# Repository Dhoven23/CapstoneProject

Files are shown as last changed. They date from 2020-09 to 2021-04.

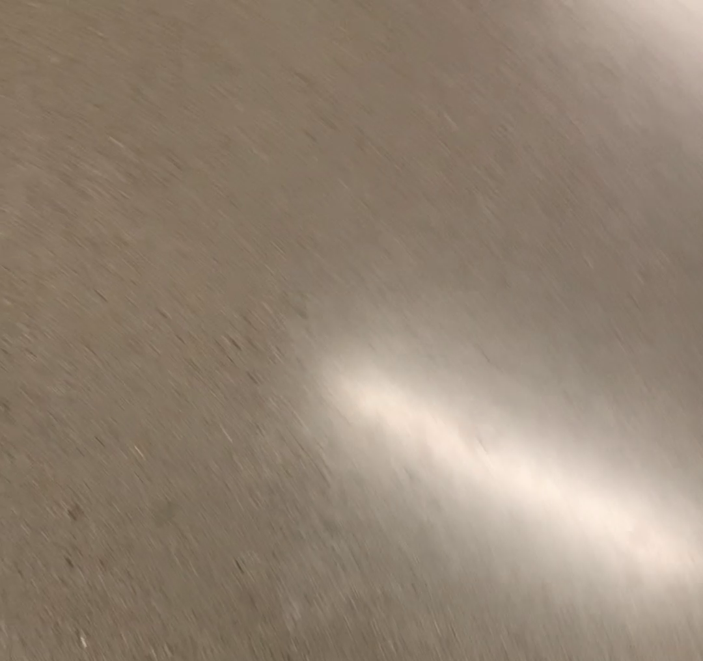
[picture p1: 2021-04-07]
src/opticalfb.png

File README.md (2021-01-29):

# CapstoneProject
Repo for Engineering capstone project

# How to use
This repository is based around the construction of a fully and partially autonomous quadcopter, mostly for educational purposes. The primary goal as a user is to solve as many problems as you feel competent to solve, and thereby improve your knowledge until you can run the vehicle entirely on your own software. Perhaps this vehicle has no advantages over existing drones, but it's far more customizable, and most importantly, its your code!

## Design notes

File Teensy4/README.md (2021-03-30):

# teensyDrone
Extension of CapstoneProject repo
For pull requests, use this version

# Usage

To use this project, you must have:

1. A Raspberry pi 4 with 8GB of memory
2. A Teensy 4.0
3. A 4 channel ESC
4. A BNO055 IMU
5. A TFMini Plus Lidar (or equivalent)
6. 4s brushless motors
7. a frame of your choice (files included)

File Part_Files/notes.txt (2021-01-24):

Here are the solidworks files for the mechanical buidl of the project. The stl's are also provided if you wish to 3D print any part. Feel free to contribute any ideas or improvements to the existing designs.

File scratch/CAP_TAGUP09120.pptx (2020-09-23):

## SPLV01 Weekly Tag Up

Presenter: Carter Senechal
Date: 091420

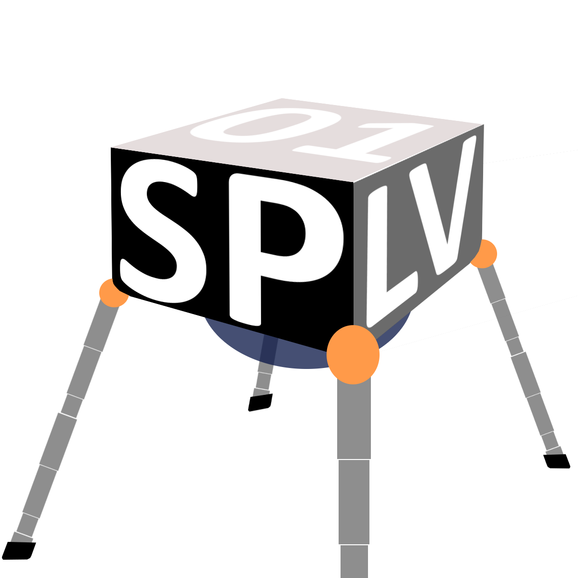
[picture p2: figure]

## Summary

- Meeting Schedule
- Upcoming deadlines
- Responsibility and Roles Hierarchy
- Open Action Items
- MBSE Design Process
- Requirements and Verification
- Jira
- Confluence

## Meeting Schedule

- Need to insert MTG schedule

## Upcoming Deadlines

## Roles and Responsibilities

Daniel Hoven
Phone: 602-696-1426
Email: Daniel.Hoven@gcu.edu
Roles: Team Leader, Chief Engineer
Responsibilities:
• Hold team members accountable to
responsibilities
• Main contributor and manager of code
base and software performance.
• Initiate and vet solutions to problem
definitions, and author technical papers
• answer technical questions, and difficult
inquiries about “big picture” items.
• Responsible for overall team progress, and
failures to meet high level deadlines

Carter Senechal
Phone: (602) 320 – 6890
Email: Cartersenechal@gmail.com
Roles: Project Manager, Systems Engineer, Electrical Engineer
Responsibilities:
• Deriving requirements from stakeholders, and extracting action plan
• Providing verification for project requirements
• Design and build electrical solutions like power and sensor circuits
• Responsible for defining completion criteria, and failures to meet low level deadlines
• POC for status / schedule / general questions

Kevin Alvarado
Phone: (805)722-0993
Email: kevinalvarado12370@gmail.com
Roles: Scheduling manager, mechanical engineer
Responsibilities:
• Responsible for coordinating team member
schedules for meetings, assignment clc’s,
and mentor meetings.
• Implement mechanical designs and
structural engineering solutions
• Responsible for reserving Lab rooms if
needed.

Dawit Feshastion
Phone :(602) 800-2549
Email: dawiterke@gmail.com
Roles: Scheduling manger, mechanical
engineer
Responsibilities:
• Responsible for the project finance
and purchasing department.
• Responsible for material quality and
simulation
• Analysis circuit and instrumental
measurement

## Roles Hierarchy

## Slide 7

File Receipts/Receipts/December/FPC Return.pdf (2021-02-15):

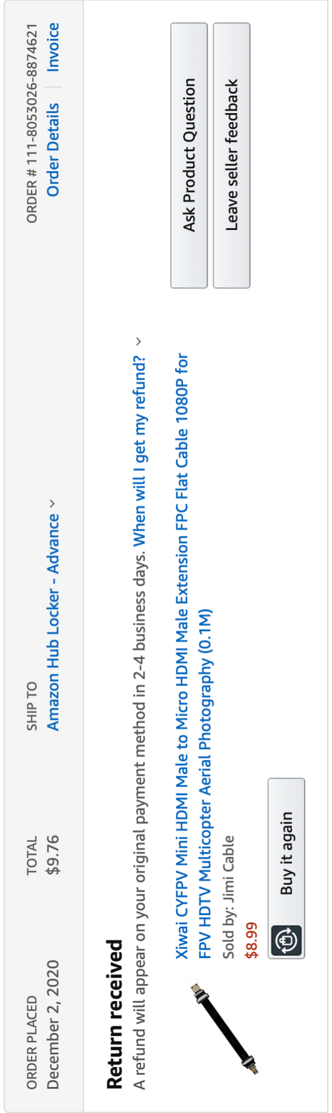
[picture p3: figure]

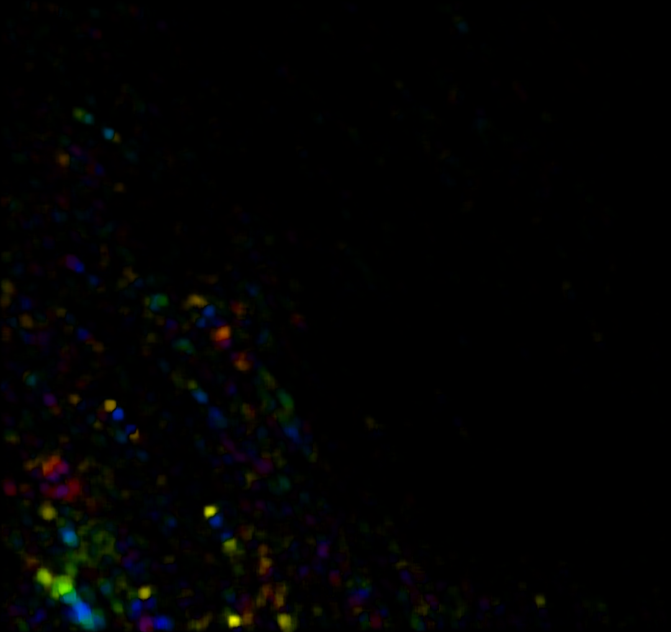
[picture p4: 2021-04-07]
src/opticalhsv.png

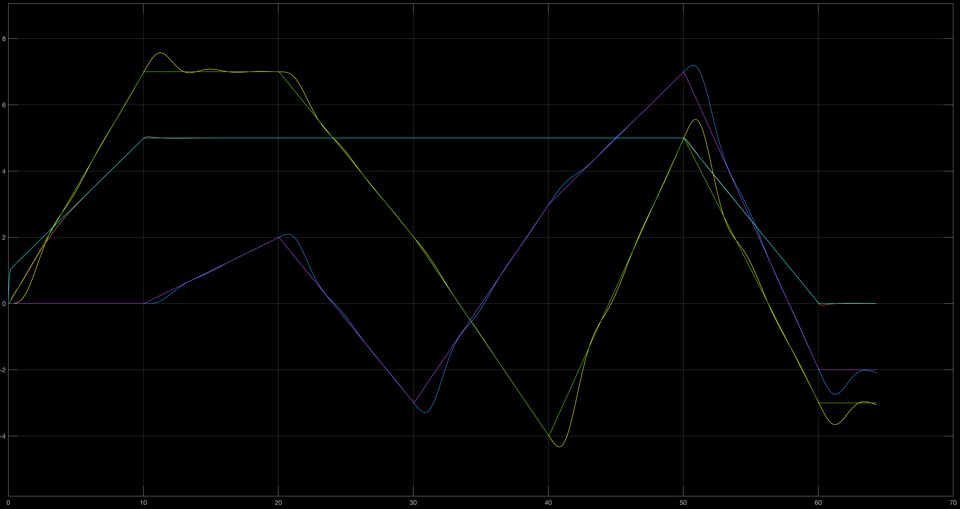
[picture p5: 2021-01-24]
MATLAB/Tracking.png

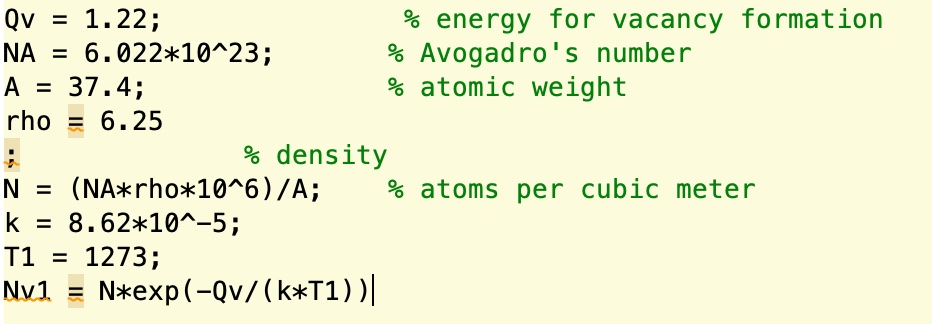
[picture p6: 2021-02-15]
Receipts/Receipts/January/sav.jpg

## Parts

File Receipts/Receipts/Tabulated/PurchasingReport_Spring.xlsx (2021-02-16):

Name | cost | number | total cost | tax | amount paid | Vendor | Date Shipped
Adafruit 9-DOF IMU BNO05 | $34.99 | 1 | $34.99 | $3.01 | $38.00 | Amazon | 2020-10-25
TOF- Lidar TFMini-s | $39.09 | 1 | $39.09 | $3.36 | $42.45 | Amazon | 2020-10-25
Raspberry Pi 4 B (8GB) | $88.86 | 1 | $88.86 | $7.64 | $96.50 | Amazon | 2020-10-22
Teensy 4.0 (/w/ pins) | $29.20 | 1 | $29.20 | $2.51 | $31.71 | Amazon | 2020-10-25
Mechanical Pro H510 Bluetooth Controller | $30.99 | 1 | $30.99 | $2.67 | $33.66 | Amazon | 2020-10-25
WayinTop Jumper wire kit for breadboard | $10.99 | 2 | $21.98 | $1.90 | $23.88 | Amazon | 2020-10-25
Crazepony EMAX 2600kv Brushless Motor (4pcs) | $50.99 | 1 | $50.99 | $4.39 | $55.38 | Amazon | 2020-11-05
Zeee 5200 mAh 50C 11.1V 3S Lipo Battery | $32.99 | 2 | $65.98 | $5.68 | $71.66 | Amazon | 2020-11-09
Aluminium Sheet 6061-T6 | $18.99 | 1 | $18.99 | $1.63 | $20.62 | Amazon | 2020-11-09
M4 Screw Assortment kit | $18.99 | 1 | $18.99 | $1.63 | $20.62 | Amazon | 2020-11-09
Maple Lumber (3/4" x 2" x 12") | $14.20 | 5 | $71.00 | $6.10 | $77.10 | Amazon | 2020-11-09
Degraw 5kg Load cell /w/ amplifier ADC | $12.99 | 4 | $51.96 | $4.48 | $56.44 | Amazon | 2020-11-09
Venom 2-8S Battery monitor | $10.99 | 1 | $10.99 | $1.01 | $12.00 | Amazon | 2020-11-09
USB C LAN adapter (thunderbolt 3 to Gigabit eth) | $17.99 | 1 | $17.99 | $1.55 | $19.54 | Amazon | 2020-11-10
NVIDIA Jetson Nano | $119.00 | 1 | $119.00 | $10.23 | $129.23 | Amazon | 2020-11-11
T300 Jetson Nano Computer Case | $28.99 | 1 | $28.99 | $4.45 | $33.44 | Amazon | 2020-11-11
Wireless-AC8265 Dual mode wireless NIC M.2E Adapter | $22.79 | 1 | $22.79 | $0.00 | $22.79 | Amazon | 2020-11-11
M6 Hex Socket Screw (304 Stainless Steel) | $7.99 | 1 | $7.99 | $0.69 | $8.68 | Amazon | 2020-11-11
Deans to XT60 adapter | $7.99 | 1 | $7.99 | $0.69 | $8.68 | Amazon | 2020-11-19
YUFAY (4CW 4CCW) Tri blae propellers | $11.99 | 1 | $11.99 | $0.00 | $11.99 | Amazon | 2020-11-16
Parallel Y splitter (battery connectors) | $13.09 | 1 | $13.09 | $0.00 | $13.09 | Amazon | 2020-11-16
62 Pcs T-Plug LiPo battery connection fittings | $15.59 | 1 | $15.59 | $0.00 | $15.59 | Amazon | 2020-11-16
30A Brushless ESC with 3A UBEC (3.5mm bullet plugs) | $16.49 | 3 | $49.47 | $0.00 | $49.47 | Amazon | 2020-11-16
Makerfocus I2C 16 channel PWM Servo Controller | $12.99 | 1 | $12.99 | $0.00 | $12.99 | Amazon | 2020-11-09
Solderable breadboards (5 pack + 1 mini board) | $11.99 | 1 | $11.99 | $0.00 | $11.99 | Amazon | 2020-11-09
30A Brushless ESC with 3A UBEC (3.5mm bullet plugs) | $16.49 | 1 | $16.49 | $0.00 | $16.49 | Amazon | 2020-11-17
Parallel Y splitter (battery connectors) | $13.09 | 1 | $13.09 | $12.46 | $25.55 | Amazon | 2020-11-16
Gold Bullet conectors (3.5mm) | $6.98 | 1 | $6.98 | $0.60 | $7.58 | Amazon | 2020-12-07
Geekworm T300 SSD/HDD Jetson Nano shields | $32.89 | 1 | $32.89 | $2.83 | $35.72 | Amazon | 2020-12-10
Mini HDMI FPC ribbon cable | $8.99 | 1 | $8.99 | $0.77 | $9.76 | Amazon | 2020-02-02
Lipo Battery Balance charger | $59.99 | 1 | $59.99 | $0.00 | $59.99 | Amazon | 2020-12-04
ESC programming card | $14.99 | 1 | $14.99 | $6.45 | $21.44 | Amazon | 2020-12-04
3D Printing Job | $6.21 | 1 | $6.21 | $0.00 | $6.21 | GCU Engineering Shop | N/A
3D Printing Job | $23.76 | 1 | $23.76 | $0.00 | $23.76 | GCU Engineering Shop | N/A
3A UBEC | $14.99 | 1 | $14.99 | $1.29 | $16.28 | Amazon | 2021-01-16
4S Batteries (14.8 V. 120 C, 2200 mAh) | $56.99 | 1 | $56.99 | $4.90 | $61.89 | Amazon | 2021-01-13
60A V2 ESC (32 bit) | $81.99 | 1 | $81.99 | $7.05 | $89.04 | Amazon | 2021-01-13
Ball End Mill (1/4" shank, 3/4" Length) | $21.99 | 1 | $21.99 | $1.89 | $23.88 | Amazon | 2021-01-14
Barometer (JBtek BMP180) | $5.99 | 1 | $5.99 | $0.52 | $6.51 | Amazon | 2021-01-14
BNO055 (Adafruit 9DOF IMU fusion) | $34.95 | 1 | $34.95 | $3.01 | $37.96 | Amazon | 2021-01-23
GoPro 50-in-1 Accessory Kit | $29.99 | 1 | $29.99 | $2.58 | $32.57 | Amazon | NYS
GoPro Hero8 (4K Waterproof camera) | $259.99 | 1 | $259.99 | $22.36 | $282.35 | Amazon | 2021-01-24
M Series Taps (Rocaris, M3 M4 M5 M6 M8, Ti Hss Flute) | $13.99 | 1 | $13.99 | $1.20 | $15.19 | Amazon | 2021-01-14
M 2.5 Standoffs (Hex brass spacer assortment) | $12.99 | 1 | $12.99 | $1.12 | $14.11 | Amazon | 2021-01-12
M3 Brass Standoffs (300 pc brass spacer assortment) | $17.99 | 1 | $17.99 | $1.55 | $19.54 | Amazon | 2021-01-23
M3 Screws (500 pc, stainless steel assortment) | $13.99 | 1 | $13.99 | $1.20 | $15.19 | Amazon | NYS
Motors (1800kV, quad) | $129.99 | 1 | $129.99 | $11.18 | $141.17 | Amazon | 2021-01-13
MPU6050 (Diymore 6DOF) | $5.99 | 1 | $5.99 | $0.52 | $6.51 | Amazon | 2021-01-14
Raspberry Pi Camera Module (V2 1080P) | $28.59 | 1 | $28.59 | $2.46 | $31.05 | Amazon | 2021-01-13
Prototyping Boards and Wire (Fermerry 10 gauge wire and AUSTOR 100 pc board kit) | $49.27 | 1 | $49.27 | $34.28 | $4.24 | Amazon | 2021-01-14
Scale (American Fristaden Lab Precision Analytical Balance 10 kg) | $119.00 | 1 | $119.00 | $10.23 | $129.23 | Amazon | 2021-01-13
Soldeirng Flux (Rosin Paste Flux 2oz) | $9.02 | 1 | $9.02 | $0.78 | $9.80 | Amazon | 2021-01-21
Teensy 4.0 (w/ pins) | $29.00 | 2 | $58.00 | $4.98 | $62.98 | Amazon | 2021-01-14
TF Mini-S LiDAR Lase Range Sensor | $41.99 | 1 | $41.99 | $3.61 | $45.60 | Amazon | 2021-01-24
Tooling Batteries (Synergy R9 Dog Collar -2x COMP 4 SAFT batteries) | $13.93 | 1 | $13.93 | $1.20 | $15.13 | Amazon | 2021-01-20
Flow Breakout Board (1597-1550-ND) | $40.80 | 1 | $40.80 | $4.08 | $44.88 | DigiKey | 2021-01-13
SD Cards (SanDisk 128GB micro) | $19.99 | 4 | $79.96 | $6.88 | $86.84 | Amazon | NYS
TOTAL: |  |  |  |  | $2315.94
BUDGET USAGE: |  |  |  |  | 57.90%

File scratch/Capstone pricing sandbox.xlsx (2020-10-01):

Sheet: big version
 | Main Battery |  | Main Computer |  | Main Power Unit | Secondary power unit
Power capacity (mAh) | 10000 | Price | $400 | part | 70 mm EDF
Voltage | 22.2 | Power Consumption (W max) | 50 | price | $65
C discharge rate | 20 | Weight (kg) | 0.75 | weight (g) | 256
price | 100 |  |  | Amperes | 69.81981982
number | 2 |  |  | power consumption (W) | 1550
weight (g) | 1320 |  |  | number | 4
instant current | 500.0 |  |  | thrust output (g) | 2500
total instant power delivery | 22200 |  |  | total mass | 1024
total price | 200 |  |  | total power consumption | 6200
total weight (kg) | 2.64 |  |  | total cost | $260
 |  |  |  | total thrust remaining (kg) | 8.976
 |  |  |  | Voltage | 22.2
TOTAL LIFT MASS (kg) | 8.976
POWER REQ. (W) | 6200
PAYLOAD REM. (kg) | 5.586
TOTAL PRICE ($) | $860
FLIGHT TIME (sec.) | 257.8064516

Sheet: Little Version (2)
 | Main Battery |  | Item List: | name: | price: | link:
Power capacity (Wh) | 33.3 |  |  | 3s LiPo battery | $60
Voltage | 11.1 |  |  | brushless motors x4 | $120
C discharge rate | 50 |  |  | ESC (30A) x4 | $60
price | $60.00 |  |  | Jetson Xavier nx | $400
number | 1 |  |  | BNO055 IMU (9 axis absolute) | $35 | https://www.amazon.com/Adafruit-Absolute-Orientation-Fusion-Breakout/dp/B017PEIGIG?cv_ct_cx=bno055
weight (g) | 175 |  |  | Carbon Fiber Sheet (3mm) | $100 | https://www.amazon.com/400x500x3-0MM-Carbon-Fiber-Sheet-Twill/dp/B085H7NX4N?hvadid=459474431166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
instant current | 150.0 |  |  | Onyx (3d printing material) 1kg | $180 | https://markforged.com/resources/blog/introducing-our-new-markforged-material-onyx
total instant power delivery (W) | 1665 |  |  | CCF for 3d printing (50cc) | $150 | https://markforged.com/materials/continuous-fibers/continuous-carbon-fiber
total price | $60.00
total weight (kg) | 0.175 |  | Total Price: |  | $1105
Amp Hours | 3
 | Main Computer
Price | $90
Teensy 4.1 MC | $30
Power Consumption (W max) | 15
Weight (kg) | 0.2
 | Main Power Unit | Secondary power unit
part | brushless motor | 30 A esc
price | $25 | $15.00
weight (g) | 52 | 20
Amperes | 13 | 25
power consumption (W) | 144.3 | 125
number | 4 | 4
thrust output (g) | 370
total weight (kg) | 0.208 | 0.08
total power consumption | 577.2 | 500
total cost | $100 | $60.00
total thrust output (kg) | 1.48
Voltage | 11.1 | 5
TOTAL MASS (kg) | 0.663
TOTAL MASS (lb.) | 1.4586
TOTAL LIFT MASS (kg) | 0.817
TOTAL LIFT MASS (lb.) | 1.7974
POWER REQ. (W) | 258.570
PAYLOAD REM. (kg) | 0.442
TOTAL PRICE ($) | $310
FLIGHT TIME (sec.) | 417.2641838
FLIGHT TIME (min.) | 7.0

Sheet: Little Version
 | Main Battery |  | Item List: | name: | price: | link:
Power capacity (Wh) | 61.05 |  |  | 3s LiPo battery | $60
Voltage | 11.1 |  |  | brushless motors x4 | $120
C discharge rate | 140 |  |  | ESC (30A) x4 | $60
price | $60.00 |  |  | Jetson Xavier nx | $400
number | 1 |  |  | BNO055 IMU (9 axis absolute) | $35 | https://www.amazon.com/Adafruit-Absolute-Orientation-Fusion-Breakout/dp/B017PEIGIG?cv_ct_cx=bno055
weight (g) | 416 |  |  | Carbon Fiber Sheet (3mm) | $100 | https://www.amazon.com/400x500x3-0MM-Carbon-Fiber-Sheet-Twill/dp/B085H7NX4N?hvadid=459474431166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
instant current | 770.0 |  |  | Onyx (3d printing material) 1kg | $180 | https://markforged.com/resources/blog/introducing-our-new-markforged-material-onyx
total instant power delivery (W) | 8547 |  |  | CCF for 3d printing (50cc) | $150 | https://markforged.com/materials/continuous-fibers/continuous-carbon-fiber
total price | $60.00 |  |  | New MacBook for Me | 1 kidney | https://www.amazon.com/gp/product/B08821611Y/ref=ox_sc_act_title_1?smid=ATVPDKIKX0DER&th=1
total weight (kg) | 0.416 |  | Total Price: |  | $1105
Amp Hours | 5.5
 | Main Computer
Price | $400
Power Consumption (W max) | 50
Weight (kg) | 0.75
 | Main Power Unit | Secondary power unit
part | 880 kv outrunner edf | 30 A esc
price | $30 | $15.00
weight (g) | 65 | 32
Amperes | 17 | 3
power consumption (W) | 188.7 | 15
number | 4 | 4
thrust output (g) | 900
total weight (kg) | 0.26 | 0.128
total power consumption | 754.8 | 60
total cost | $120 | $60.00
total thrust output (kg) | 3.6
Voltage | 11.1 | 5
TOTAL MASS (kg) | 1.554 | 3.42597948
TOTAL LIFT MASS (kg) | 2.046 | 2.267964547
POWER REQ. (W) | 540.1548387
PAYLOAD REM. (kg) | 0.88
TOTAL PRICE ($) | $640
FLIGHT TIME (sec.) | 406.8833309

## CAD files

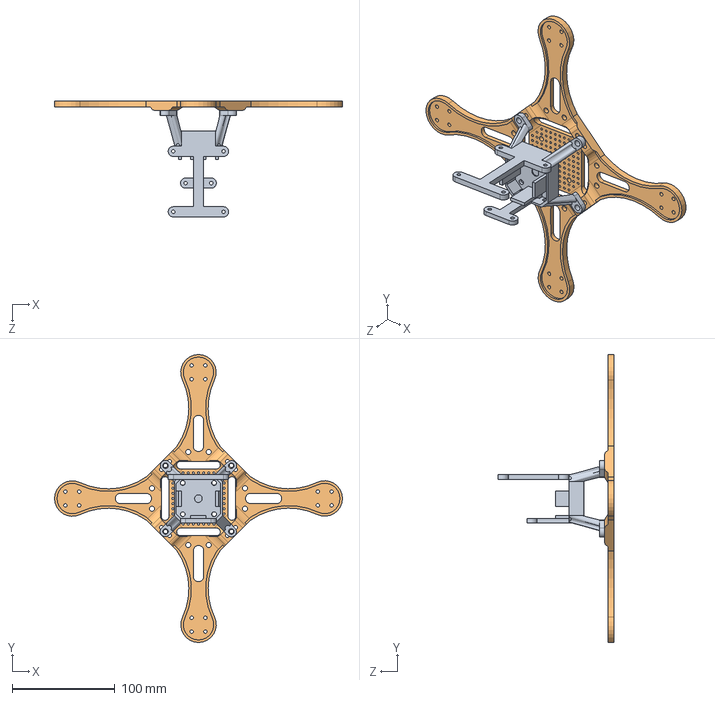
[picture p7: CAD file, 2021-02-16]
Part_Files/Drone 2.0/Assem2.SLDASM
280.7 x 280.7 x 113.0 mm
Superstructure
base plate (Revised holes)

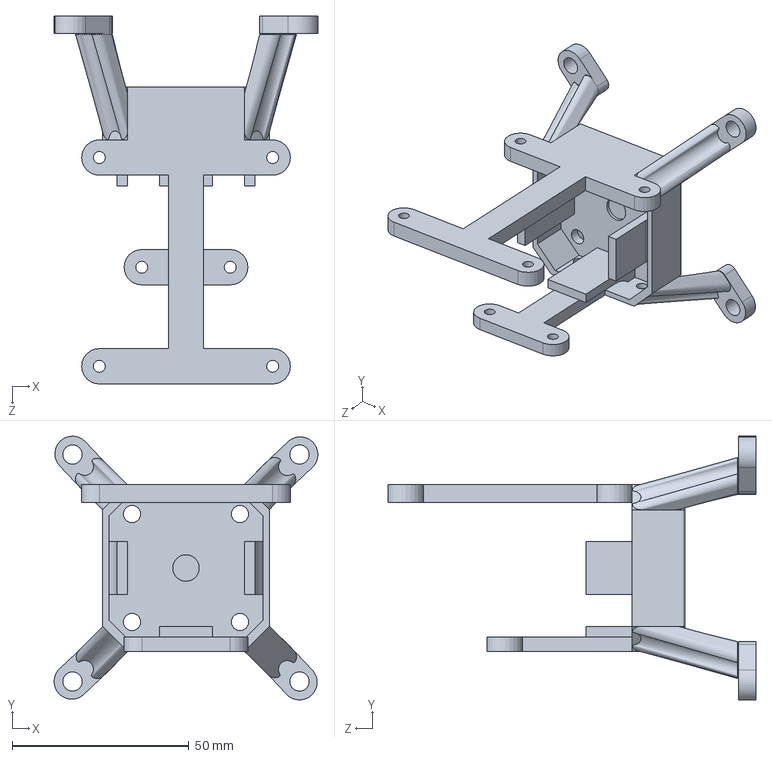
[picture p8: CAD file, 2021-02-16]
Part_Files/Drone 2.0/Superstructure.SLDPRT
74.5 x 74.5 x 104.0 mm

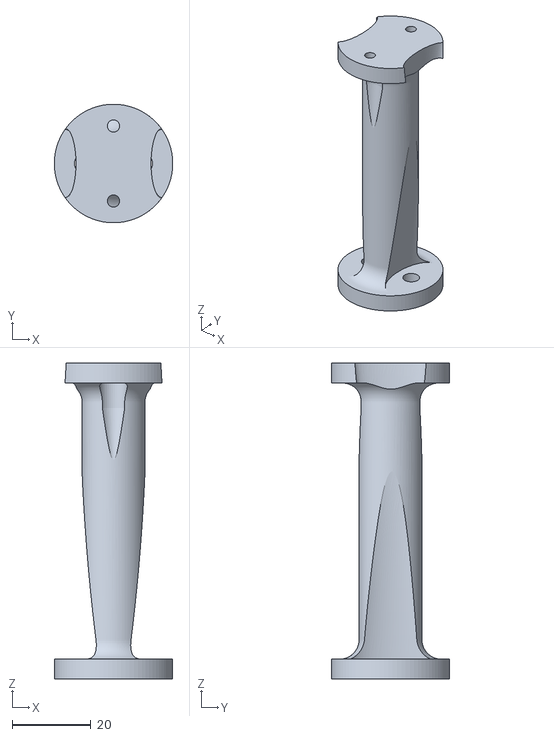
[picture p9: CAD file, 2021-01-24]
Part_Files/Drone 2.0/Force_cell_standoff.STL
30.0 x 30.0 x 80.0

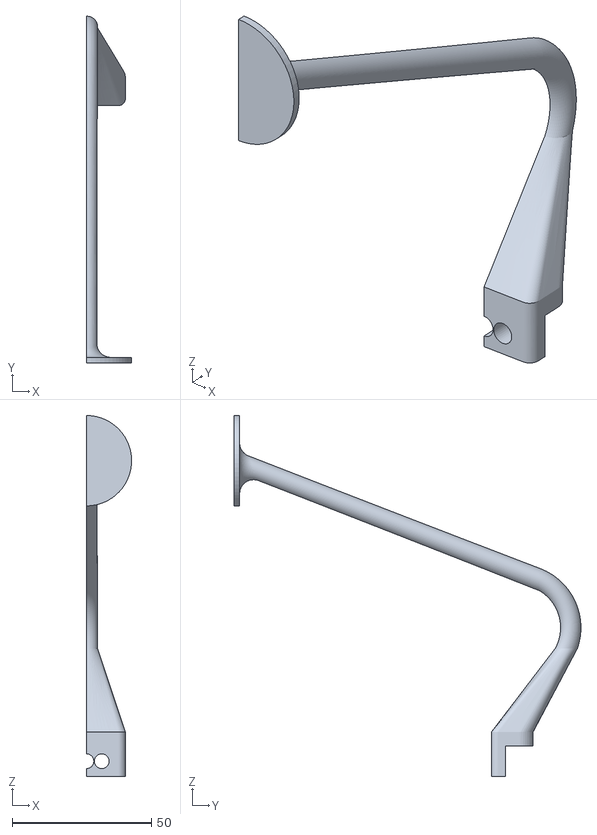
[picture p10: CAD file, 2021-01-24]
Part_Files/Drone 2.0/landing leg1.STL
16.2 x 124.7 x 129.8

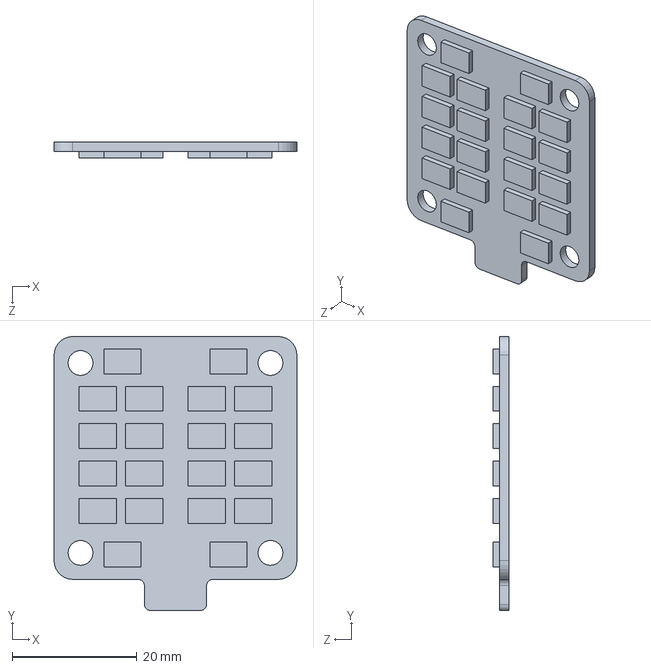
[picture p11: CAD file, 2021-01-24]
Part_Files/Drone 2.0/esc.SLDPRT
39.0 x 44.0 x 2.50 mm

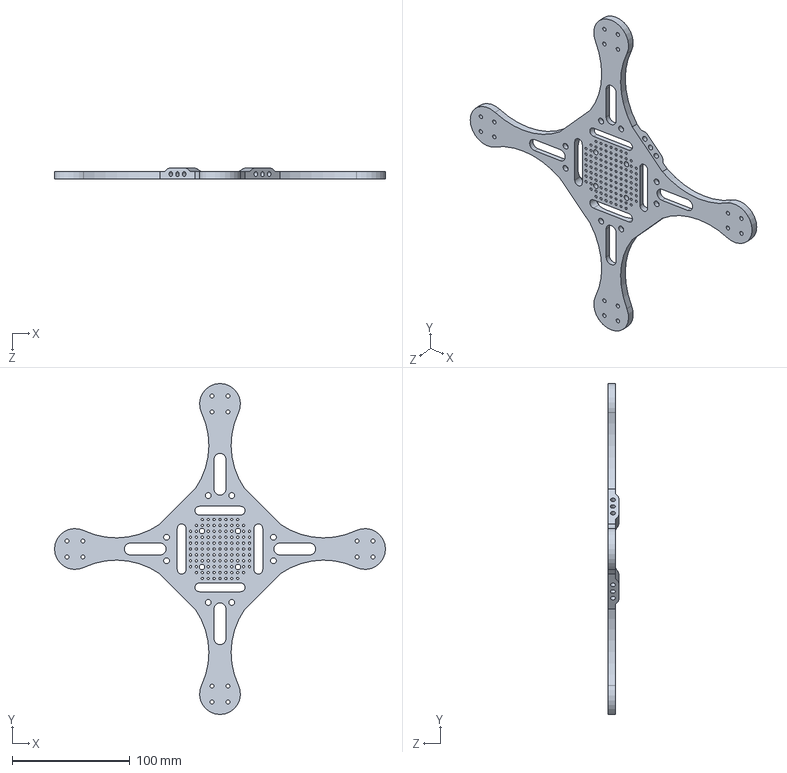
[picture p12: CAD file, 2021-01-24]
Part_Files/Drone 2.0/base plate.SLDPRT
280.7 x 280.7 x 9.00 mm

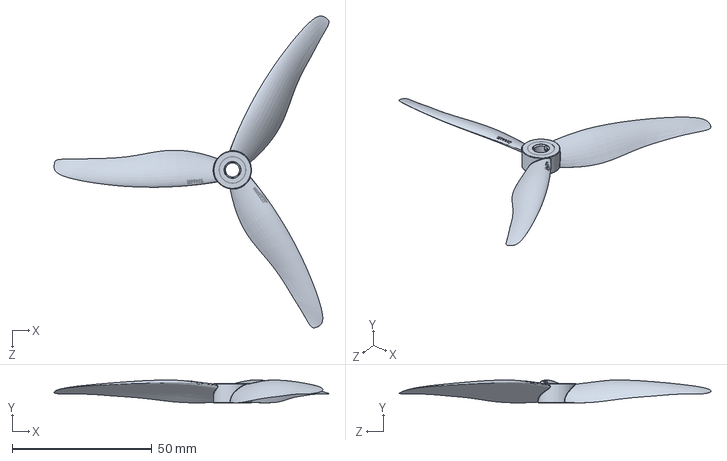
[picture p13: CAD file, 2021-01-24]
Part_Files/Drone 2.0/fan.SLDPRT
98.5 x 8.23 x 111.7 mm

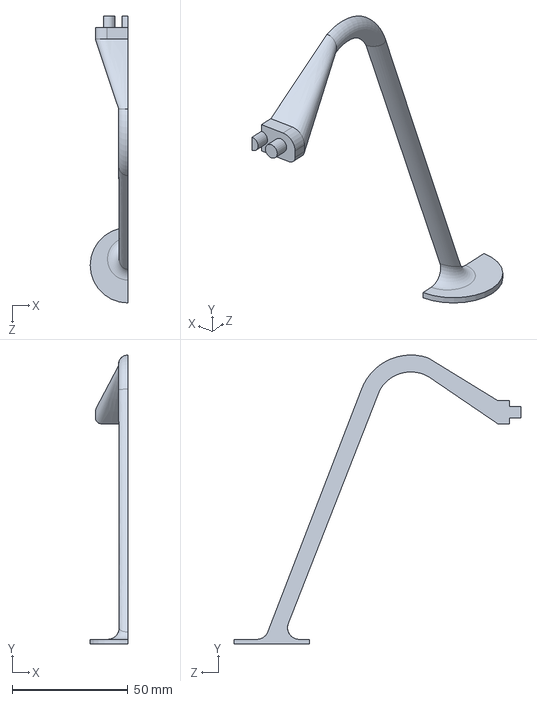
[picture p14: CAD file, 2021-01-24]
Part_Files/Drone 2.0/landing leg2.SLDPRT
16.2 x 124.7 x 123.8 mm

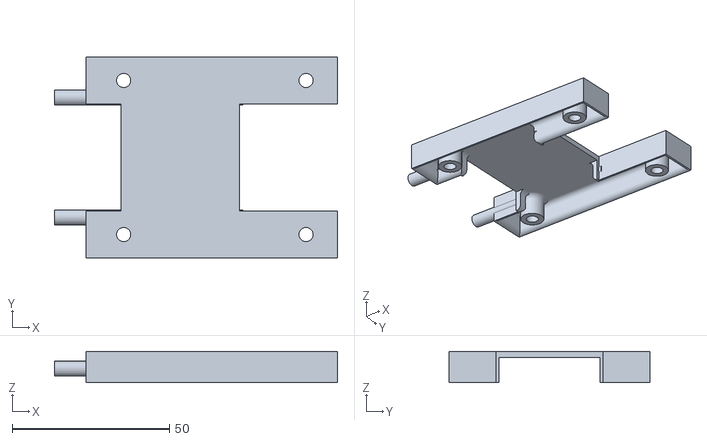
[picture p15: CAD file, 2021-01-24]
Part_Files/Drone 2.0/pi backing.STL
90.0 x 64.0 x 10.0

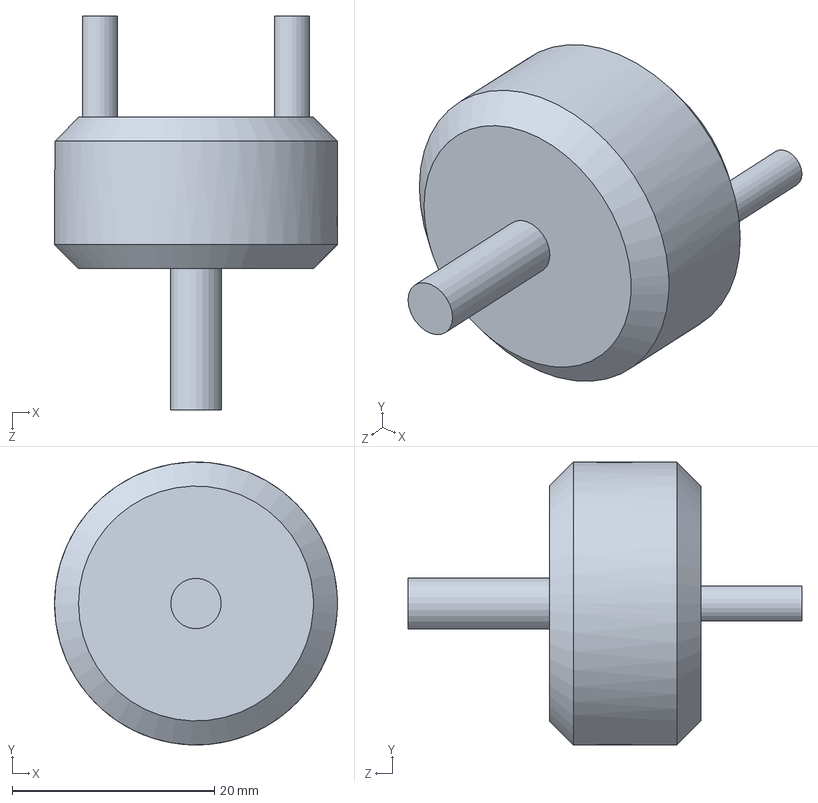
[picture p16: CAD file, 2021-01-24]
Part_Files/Drone 2.0/motor exclusion.SLDPRT
28.0 x 28.0 x 39.0 mm

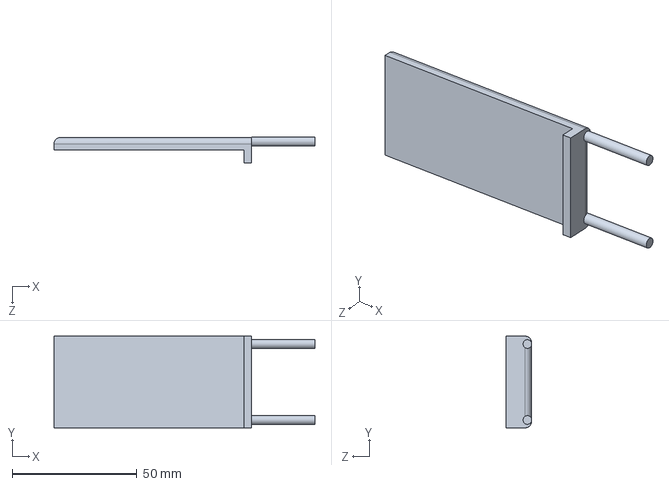
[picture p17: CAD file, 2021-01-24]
Part_Files/Drone 2.0/pcb back.SLDPRT
104.8 x 36.8 x 10.3 mm

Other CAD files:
Part_Files/Drone 2.0/landing leg.SLDPRT
Part_Files/Drone 2.0/force_ce.SLDPRT
Part_Files/Drone 2.0/Superstructure.STL
Part_Files/Drone 2.0/base plate.STL
Part_Files/Drone 2.0/landing leg.STL
Part_Files/Drone 2.0/landing leg2.STL

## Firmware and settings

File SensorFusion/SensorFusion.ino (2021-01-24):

/* This code is free and open source. I only ask that if you use my code in an academic setting, reference it appropriately. 
*  I mean, an extra citation can't hurt can it?
* 
* Author: Daniel Hoven
* Univeristy: Grand Canyon University
* Email: Daniel.Hoven@gcu.edu
*/

/* This code is for sensor fusion of IMU data with barometric altitude 
 *  and accelerometer data for odometric calculation of position. 
 */

// This code relies on the Adafruit Unified Sensor Library

#include <Wire.h>
#include <Adafruit_BMP085.h>
#include <Adafruit_Sensor.h>
#include <Adafruit_BNO055.h>
#include <Adafruit_MPU6050.h>
#include <utility/imumaths.h>


// Adafruit Sensors Initialize
Adafruit_BMP085 bmp;
Adafruit_BNO055 bno = Adafruit_BNO055(55, 0x28);
Adafruit_MPU6050 mpu;


// Declare ext. vars
float acc_x = 0,
      acc_y = 0,
      acc_z = 0,
      vel_x = 0,
      vel_y = 0,
      vel_z = 0,
      pos_x = 0,
      pos_y = 0,
      pos_z = 0,
      alt = 0, 
      alt_old = 0, 
      off_set = 0,
      q0,
      q1,
      q2,
      q3,
      av_alt[10],
      C[4];

float gravity_quaternion[4] = {0, 0, 0, 10.1};

      
// Declare Processor dependent vars.       
volatile float _q0 = 0, 
               _q1 = 1, 
               _q2 = 0, 
               _q3 = 0;
  
void setup() {
  
  Serial.begin(115200);
  delay(100);

  // Initialize Barometer
  if (!bmp.begin()) {
	  Serial.println("Could not find a valid BMP085 sensor, check wiring!");
	  while (1) {
	    delay(10);
	    }
  }

  // Initialize Accelerometer
  if (!mpu.begin()) {
    Serial.println("Failed to find MPU6050 chip");
    while (1) {
      delay(10);
    }
  }

  // Initialize IMU
  if (!bno.begin())
  {
    /* There was a problem detecting the BNO055 ... check your connections */
    Serial.print("Ooops, no BNO055 detected ... Check your wiring or I2C ADDR!");
    while (1){
      delay(10);
    }
  }

  //Set Accelerometer limits
  mpu.setAccelerometerRange(MPU6050_RANGE_8_G);
  mpu.setGyroRange(MPU6050_RANGE_500_DEG);
  mpu.setFilterBandwidth(MPU6050_BAND_21_HZ);
  
  // Get Baseline alititude
  delay(500);
  off_set = bmp.readAltitude(101500);
  delay(1000);
}

  
void loop() {
   
    ReadBarometricAltitude();
    get_IMU_sample();
    get_Accels();

    
    // math for gravity correction
    q0 = _q0;
    q1 = _q1;
    q2 = _q2;
    q3 = _q3;
    
    float gamma  = -atan2(2.0 * (q3 * q2 + q0 * q1) , 1.0 - 2.0 * (q1 * q1 + q2 * q2));// * (180/PI);
    float beta = asin(2.0 * (q2 * q0 - q3 * q1));// * (180/PI);
    float alpha   = -atan2(2.0 * (q3 * q0 + q1 * q2) , - 1.0 + 2.0 * (q0 * q0 + q1 * q1));// * (180/PI);

    float RotationMatrix[3][3];
    
          RotationMatrix[0][0] = cos(alpha)*cos(beta);
          RotationMatrix[1][0] = cos(alpha)*sin(beta)*sin(gamma) - sin(alpha)*cos(gamma);
          RotationMatrix[2][0] = cos(alpha)*sin(beta)*cos(gamma) + sin(alpha)*sin(gamma);
          RotationMatrix[0][1] = sin(alpha)*cos(beta);
          RotationMatrix[1][1] = sin(alpha)*sin(beta)*sin(gamma) + cos(alpha)*cos(gamma);
          RotationMatrix[2][1] = sin(alpha)*sin(beta)*cos(gamma) - cos(alpha)*sin(gamma);
          RotationMatrix[0][2] = -sin(beta);
          RotationMatrix[1][2] = cos(beta)*sin(gamma);
          RotationMatrix[2][2] = cos(beta)*cos(gamma);

//          for(int i=0;i<3;i++){
//            Serial.print("| ");
//            for(int j=0;j<3;j++){
//              Serial.print(RotationMatrix[i][j]),Serial.print(' ');
//            }
//            Serial.println(" |");
//          }

    

    float gravity[3] = {0, 0, 1},
          rot_quat[4] = {q0, q1, q2, q3},
          rot_quat2[4] = {q0,-q1,-q2,-q3},
          rot_gravity[4],
          acc_quat[4] = {0,acc_x,acc_y,acc_z};
                      
          
      
    // Rotate Gravity
    HamiltonProduct(rot_quat, gravity_quaternion);
    HamiltonProduct(C,rot_quat2); 

    // Store output
    for(int i=0;i<4;i++){
      rot_gravity[i] = C[i];
    }

    // Rotate Acceleration
    HamiltonProduct(rot_quat, acc_quat);
    HamiltonProduct(C,rot_quat2);

    for(int i=0;i<4;i++){
      acc_quat[i] = C[i];
    }
    
    
    //acc_x-=rot_gravity[1]; // Remove Gravity (i)
    //acc_y-=rot_gravity[2]; // Remove Gravity (j)
    //acc_z-=rot_gravity[3]; // Remove Gravity (k)

    

    Serial.print(" gravity.x "),Serial.print(rot_gravity[1],2);
    Serial.print(" gravity.y "),Serial.print(rot_gravity[2],2);
    Serial.print(" gravity.z "),Serial.println(rot_gravity[3],2);
    Serial.print(" acc.x: "),Serial.print(acc_x);
    Serial.print(" acc.y: "),Serial.print(acc_y);
    Serial.print(" acc.z: "),Serial.println(acc_z);
    Serial.print(" roll: "),Serial.print(gamma);
    Serial.print(" pitch: "),Serial.print(beta);
    Serial.print(" yaw: "),Serial.println(alpha);
    
    
    //Serial.print(", Alt: "),Serial.print(alt*100),Serial.println(" cm");
    
    delay(10);
}


void get_IMU_sample() {
  /* get quaternions */
  imu::Quaternion quat = bno.getQuat();
  

  _q0 = quat.w();
  _q1 = quat.x();
  _q2 = quat.y();
  _q3 = quat.z();
  
}

void ReadBarometricAltitude(){
  
    alt = bmp.readAltitude(101500) - off_set;
    
    float num = 0;
    
    for(int i = 0;i<9;i++){ av_alt[i] = av_alt[i+1]; num+=av_alt[i];}
    
    av_alt[9] = alt;
    num+=alt;
    alt=num/50; 
    
    
}

void get_Accels(){

    sensors_event_t a, g, temp;
    mpu.getEvent(&a, &g, &temp);
 
    acc_x = a.acceleration.x;
    acc_y = a.acceleration.y;
    acc_z = a.acceleration.z;
}

void HamiltonProduct(float A[4], float B[4]){

    float a1 = A[0], //input quaternion A
          a2 = A[1], // (i)
          a3 = A[2], // (j)
          a4 = A[3]; // (k)

    float b1 = B[0], //input quaternion B
          b2 = B[1], // (i)
          b3 = B[2], // (j)
          b4 = B[3]; // (k)
          
    
    float c1 = a1*b1 - a2*b2 - a3*b3 - a4*b4, // Output Quaternion (w)
          c2 = a1*b2 + a2*b1 + a3*b4 - a4*b3, // Output Quaternion (i)
          c3 = a1*b3 - a2*b4 + a3*b1 + a4*b2, // Output Quaternion (j)
          c4 = a1*b4 + a2*b3 - a3*b2 + a4*b1; // Output Quaternion (k)
          
    C[0] = c1;
    C[1] = c2;
    C[2] = c3;
    C[3] = c4;

}

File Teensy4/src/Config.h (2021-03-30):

/* =========================================================================================
  Define controller constants */

#define THROTTLE_SCALER 0.5
#define kp 2                               // Altitude PID proportional constant 
#define ki 0                              // Altitude PID integral constant
#define kd 0.01                          // Altitude PID derivative constant
#define filtAlt 0.95                    // Altitude Estimation Filter constant (0-1)
#define LQRmult 0.45                   // Scaling factor for control law, varies between 0.5-1
#define LQR_P 0                     // LQR_P constant proportional prescaler
#define LQR_E 1.75                   // Integrator prescaler
#define INTEGRATOR_CLAMP 0.175      // Clamping term for integrator 
#define SLEW_LIMIT 10              // controller gimbal limit (higher = faster vehicle)
#define SLEW_FILTER 0.25           // Controller rate limiter (0-1), higher = slower/stabler
#define D_COMP 0.1             // dynamic damping coefficient. higher = more dynamic, lower = more damping
#define V_SPD 0.01              // Vertical speed reduction rate (depends on iteration time, faster code = lower value, typically 0.001-0.01)
#define DERIVATIVE_FILT 0.75   // Fintering term for low pass derivative filter

/* ==========================================================================================
  Define communication setup
*/
#ifndef RADIO_BAUDRATE
#define RADIO_BAUDRATE 57600    // Telemetry radio baudrates (use 57600)
#endif

#define LIDAR_BAUDRATE 115200   // LiDAR sensor UART speed. default is 115200

#ifndef USB_BAUDRATE
#define USB_BAUDRATE 250000     // USB Serial port baudtate. (N/A for USB mode)
#endif

#ifndef SERIAL_USB
#define SERIAL_USB Serial       // Serial port for USB communication (always Serial)
#endif

#ifndef RADIO_SERIAL
#define RADIO_SERIAL Serial4    // Serial port for radio communication
#endif

#ifndef LIDAR_SERIAL
#define LIDAR_SERIAL Serial1    // Serial port for LiDAR sensor
#endif

#define CMD_SERIAL Serial      // Listen port for waypoints
#define TELEMETRY1 Serial4     // wireless telemetry
#define TELEMETRY2 Serial      // wired telemetry

/* ==========================================================================================
  Define motor setup */

#define ESC1 6         // Pin for ESC1
#define ESC2 7         // Pin for ESC2
#define ESC3 5         // Pin for ESC3
#define ESC4 4         // Pin for ESC4
#define MAXVAL 1500    // highest speed controller may command esc
#define MINVAL 900     // lowest speed controller may command esc (other than 0)
#define IDLE_SPEED 20  // idle motor speed, range 12-20 ish, depending on esc calibration

#define E1CENTER 1         // Pin for ESC1
#define E2CENTER 1         // Pin for ESC2
#define E3CENTER 1         // Pin for ESC3
#define E4CENTER 1         // Pin for ESC4

/* Set the delay between iterations */
#define MAIN_DELAY 1

/* Define LQR gain matrix.
The rows define the inputs (U) to each Output value
The columns are the Full state (X) of the Vehicle
The linear math here is: 
                X' = AX 
                + K(R-X) 
                + K(R-Xint)

The Expansion of U is:
                        U[0] = total vehicle thrust
                        U[1] = moment about the X axis
                        U[2] = moment about the y axis
                        U[3] = moment about the z axis

So to "tune" and axis, say x, find the corresponding row, 
in this case the second row, and alter the values 
to choose how the moment about that axis is related to 
the respective columns of the vehicles state. (Curently the values
represent response to angular position about X, and angular speed about X)
*/

double K [4][6] = {{
    0, 0, 0, 0, 0, 0,
  }, {
    15, 0, 0, -100, 0, 0,
  }, {
    0, 15, 0, 0, -100, 0,
  }, {
    0, 0, 15, 0, -30, 0,
  },
};

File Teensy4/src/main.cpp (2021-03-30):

#include <Arduino.h>
#include "SensorFunctions.h"

/* --------------------------------------------------------------------------------------
  Main Controller Code to run on Teensy 4.0
  Author: Daniel Hoven Date: 3/15/2021 Project: Senior Capstone
  --------------------------------------------------------------------------------------*/
/*= == == == == == == == == == == == == == == == == == == == == == == == == == == == == == == == == = == == == == == == == =
SETUP 
*/

void setup()

{
  /* Open Serial Ports*/

  SERIAL_USB.begin(250000);
  LIDAR_SERIAL.begin(115200);
  RADIO_SERIAL.begin(RADIO_BAUDRATE);
  delay(100);

  /* put liDAR in std. output mode */

  set_liDAR();

  while (!bno.begin())
  {
    /* There was a problem detecting the BNO055 ... check your connections */
    SERIAL_USB.print("Ooops, no BNO055 detected ... Check your wiring or I2C ADDR!");
    delay(200);
  }

  SERIAL_USB.print("IMU found\n");
  bno.setExtCrystalUse(true);

  for (int i = 0; i < 4; i++)
  {
    for (int j = 0; j < 6; j++)
    {
      K[i][j] *= LQRmult;
    }
  }

  calibrateESCs();
  delay(500);
}

/*-------------------------------------------------------------------------------
   main
  ------------------------------------------------------------------------------*/
void loop(void)
{

  global.dt = micros() - global.tMicros;
  global.tMicros = micros();
  global.dt = global.dt / 1000000;

  get_IMU_sample(global.dt,global.iterations),
  get_Distance_sample(global.dt),
  ELQR_calc();

  if (global.VERT_SPEED == true)
  {
    vertSpeedHold();
  }
  receiveData();

  if (global.iterations % 5 == 0)
  {
    printData();
    //printTestData();
  }

  // Make sure Vehicle isn't dying
void CheckAttitudeLimits(); // Oh Sh*t method

  if ((global.TAKEOFF_FLAG) && (millis() > 2000))
  {
    IntegralTracker(global.dt);
    AltitudePID();
  }

  if (global.iterations < 1000)
  {
    for (int i = 1; i < 4; i++)
    {
      signal.Ucal[i] = signal.U[i];
    }
  }
  else
  {
    if (!global.STOP_FLAG)
    {
      commandESCs();
    }
    else
    {
      STOP();
    }
  }
  global.iterations++;
  delay(MAIN_DELAY);
}

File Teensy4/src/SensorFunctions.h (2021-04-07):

#include "Config.h"
#include "Arduino.h"
#include <Wire.h>
#include <Adafruit_Sensor.h>
#include <Adafruit_BNO055.h>
#include <utility/imumaths.h>
#include <avr/io.h>
#include <avr/interrupt.h>
#include <Servo.h>

/* ==========================================================================================
  Declare globals */

struct Signal
{
  float e1 = 0,
        e2 = 0,
        e3 = 0,
        e4 = 0,
        Ecal[4] = {0, 0, 0, 0};
  
  int throttle = 0;

  double U[4] = {IDLE_SPEED, 0, 0, 0},
         Ucal[4];

};

volatile float liDARold = 0,
               _lidar = 0;

volatile int liDARval = 0,
             strength = 0;

struct Euler
{
  double x = 0,
         y = 0,
         z = 0;

  double dx = 0,
         dy = 0,
         dz = 0;

  double Hist[3][5];
};

struct State
{
  double Full[6] = {0, 0, 0, 0, 0, 0},
         Integral[6],
         Old[6],
         Error[6];
};

struct Altitude
{
  double alt = 0,
         d_alt = 0,
         initAlt = 0;
};

struct Setpoint
{
  double R[6] = {0, 0, 0, 0, 0, 0};
  double Alt = 0;
  double Rcal[3] = {0, 0, 0};
  double verticalSpeed = 0;
};

struct Global
{
  long int iterations = 0;
  int tMicros = 0;
  double dt = 0;

  String STATE = "STARTUP";

  bool STOP_FLAG = false,
       TAKEOFF_FLAG = false,
       VERT_SPEED = true;
};

float Ncode;
u_int16_t counter = 0;

String STATE = "STARTUP";

char Dcode[3];

State X;           // Vehicle Full state struct
Euler euler;       // Euler angle struct
Setpoint setPoint; // setpoint struct
Altitude altitude; // altitude data
Signal signal;     // controller output data
Global global;

/* =========================================================================================
  Declare Sensor Connections on I2C bus
*/

Adafruit_BNO055 bno = Adafruit_BNO055(55, 0x28);

Servo esc1,
    esc2,
    esc3,
    esc4;

/*-------------------------------------------------------------------------
   Write external functions
  ---------------------------------------------------------------------------*/

void set_liDAR()
{
  LIDAR_SERIAL.write(0x42);
  LIDAR_SERIAL.write(0x57);
  LIDAR_SERIAL.write(0x02);
  LIDAR_SERIAL.write(0x00);
  LIDAR_SERIAL.write(0x00);
  LIDAR_SERIAL.write(0x00);
  LIDAR_SERIAL.write(0x01);
  LIDAR_SERIAL.write(0x06);
}

void calibrateESCs()
{

  esc1.attach(ESC1);
   esc2.attach(ESC2);
    esc3.attach(ESC3);
     esc4.attach(ESC4);
      delay(100);
     esc1.write(30);
    esc2.write(30);
   esc3.write(30);
  esc4.write(30);
  delay(1000);

  for (int i = 30; i > 20; i--)
  {
    esc1.write(i);
    esc2.write(i);
    esc3.write(i);
    esc4.write(i);
  }

  for (int i = 20; i < 35; i++)
  {
    esc1.write(i);
    esc2.write(i);
    esc3.write(i);
    esc4.write(i);
    delay(150);
  }
  delay(2000);
  esc1.write(40);
  esc2.write(40);
  esc3.write(40);
  esc4.write(40);
  delay(2000);
}

FASTRUN void get_IMU_sample(double dt, double iterations)
{

  /* get quaternions */

  imu::Quaternion quat = bno.getQuat();

  volatile double q0 = quat.w();
  volatile double q1 = quat.x();
  volatile double q2 = quat.y();
  volatile double q3 = quat.z();

  //quaternion conversion

  euler.x = (-setPoint.Rcal[0]) - atan2(2.0 * (q3 * q2 + q0 * q1), 1.0 - 2.0 * (q1 * q1 + q2 * q2));  //* (180/PI);
  euler.y = (-setPoint.Rcal[1]) + asin(2.0 * (q2 * q0 - q3 * q1));                                    // * (180/PI);
  euler.z = (-setPoint.Rcal[2]) - atan2(2.0 * (q3 * q0 + q1 * q2), -1.0 + 2.0 * (q0 * q0 + q1 * q1)); //* (180/PI);

  for (int i = 0; i < 6; i++)
  {
    X.Old[i] = X.Full[i];
  }

  X.Full[0] = euler.x;
  X.Full[1] = euler.y;
  X.Full[2] = euler.z;

  // Compute Derivatives using 5 point stencil
  double h = dt;
  for (int i = 0; i < 3; i++)
  {
    for (int j = 1; j < 5; j++)
    {
      euler.Hist[i][j] = euler.Hist[i][j - 1];
    }
    euler.Hist[i][0] = X.Full[i];
    double temp;
    temp = (-1) * euler.Hist[i][0] + (8) * euler.Hist[i][1] + (-8) * euler.Hist[i][3] + (1) * euler.Hist[i][4];
    temp /= 12 * h;
    if (iterations > 5)
    {
      X.Full[i + 3] = DERIVATIVE_FILT * X.Old[i + 3];
      X.Full[i + 3] += (1 - DERIVATIVE_FILT) * temp;
    }
    else
    {
      X.Full[i + 3] = .1; // prime derivatives with nonzero values
    }
  }
}

void get_Distance_sample(double dt)
{

  if (LIDAR_SERIAL.available() >= 9) // When at least 9 bytes of data available (expected number of bytes for 1 signal), then read
  {
    if ((0x59 == LIDAR_SERIAL.read()) && (0x59 == LIDAR_SERIAL.read())) // byte 1and byte 2
    {
      unsigned int t1 = LIDAR_SERIAL.read(); // byte 3 = Dist_L
      unsigned int t2 = LIDAR_SERIAL.read(); // byte 4 = Dist_H
      t2 <<= 8;
      t2 += t1;
      liDARval = t2;
      t1 = LIDAR_SERIAL.read(); // byte 5 = Strength_L
      t2 = LIDAR_SERIAL.read(); // byte 6 = Strength_H
      t2 <<= 8;
      t2 += t1;
      strength = t2;
      for (int i = 0; i < 3; i++)
        LIDAR_SERIAL.read(); // ignore remaining bytes
    }
  }
  _lidar = (1 - filtAlt) * liDARval + filtAlt * liDARold;
  liDARold = _lidar;
  double _alt = _lidar * cos(euler.x) * cos(euler.y);
  altitude.d_alt *= filtAlt;
  altitude.d_alt += (1 - filtAlt) * (_alt - altitude.alt) / dt;
  altitude.alt = _alt;
}

FASTRUN void DerivativeComp()
{
  for (int i = 0; i < 3; i++)
  {
    setPoint.R[i + 3] = D_COMP * (X.Full[i] - setPoint.R[i]);
  }
}

FASTRUN void ELQR_calc()
{

  for (int i = 1; i < 4; i++)
  {
    double iter = 0;
    for (int j = 0; j < 3; j++)
    {
      iter += K[i][j] * ((X.Full[j] - setPoint.R[j]) + LQR_E * (X.Integral[j]));
    }
    for (int j = 3; j < 6; j++)
    {
      iter += K[i][j] * ((X.Full[j] - setPoint.R[j]) + LQR_P * (X.Integral[j]));
    }
    if (abs(iter) < SLEW_LIMIT)
    {
      signal.U[i] = iter;
      signal.U[i] -= signal.Ucal[i];
    }
    else if (iter > 0)
    {
      signal.U[i] = SLEW_LIMIT;
    }
    else if (iter < 0)
    {
      signal.U[i] = -SLEW_LIMIT;
    }
  }
}

FASTRUN void IntegralTracker(double dt)
{

  for (int i = 0; i < 3; i++)
  {
    double iter = (dt / 2) * (X.Old[i] + X.Full[i]);
    if ((abs(iter) + abs(X.Integral[i])) < INTEGRATOR_CLAMP)
    {
      X.Integral[i] += iter;
      X.Integral[i + 3] = X.Full[i];
    }
    else if ((iter + X.Integral[i]) < -INTEGRATOR_CLAMP)
    {
      X.Integral[i] += 0.01;
      X.Integral[i + 3] = X.Full[i];
    }
    else if ((iter + X.Integral[i]) > INTEGRATOR_CLAMP)
    {
      X.Integral[i] -= 0.01;
      X.Integral[i + 3] = X.Full[i];
    }
  }
  for (int i = 0; i < 3; i++)
  {
    if (abs(X.Integral[i] - setPoint.R[i]) > INTEGRATOR_CLAMP)
    {
      if ((X.Integral[i] - setPoint.R[i]) > 0)
      {
        X.Integral[i] = INTEGRATOR_CLAMP + setPoint.R[i] - 0.01;
      }
      else if ((X.Integral[i] - setPoint.R[i]) < 0)
      {
        X.Integral[i] = -(INTEGRATOR_CLAMP + setPoint.R[i]) + 0.01;
      }
    }
  }
}

bool goingToCrash()
{
  return false;
}
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

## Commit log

2020-09-12 init commit
    [Capstone pricing sandbox.xlsx]
2021-01-05 clean directory
    [Capstone pricing sandbox.xlsx]
2021-01-21 add sensor fusion
2021-01-22 fix Sensor Fusion
2021-01-24 Add files via upload
    Solidworks files + stl's
    [Force_cell_standoff.STL, base plate.SLDPRT, base plate.STL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]
2021-01-24 add Teensy 4.0 files
2021-02-15 purchasing report
    [PurchasingReport.xlsx]
2021-02-15 add reciepts and BOM's
    [PurchasingReport.xlsx]
2021-02-16 Spring purchasing list
    [PurchasingReport_Spring.xlsx]
2021-02-16 add new vehicle
    [Assem1.SLDASM, Assem2.SLDASM, Force_cell_standoff.STL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]
2021-03-05 current stash
2021-03-14 Platform IO rebuild
    [Book1.xlsx, Flight Data.csv, batteryDrainDarta.xlsx]
2021-03-30 fix proportional constants
    [Flight2Data.csv, throttle.csv]
2021-03-30 rebase directory
    [screen.csv]
2021-04-07 final presentation
    [hardenability.xlsx]
